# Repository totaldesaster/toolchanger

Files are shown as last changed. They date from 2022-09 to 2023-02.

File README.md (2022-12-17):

# Low-Cost Open Source Toolchanging mechanism for 3D printers

Magnetic tool changer project, inspired by E3D and Jubilee tool changing printers and designed for low cost and wide compatibility. My goal is to make toolchanging accessible without owning four figure machines.

# How does it work?




Both the tools and the toolhead have a circle of neodymium magnets with alternating north/south up polarities. Since opposing poles attract and same poles repel, the machine can switch between pulling and pushing on the tool by aligning the opposing or same poles of the magnets. This is done by a geared stepper motor on the toolhead which rotates the magnet circle (lockplate) - marked red and blue for north and south up in the first picture. Steel balls on the head and L profiles on the tool form a Maxwell coupling which ensures repeatable connections by having the tool contact the head in exactly 6 points - eliminating all 6 degrees of freedom, but not overconstraining the assembly, so there is theoretically exactly one position the tool can be in. The Klipper firmware is capable of controlling such a setup using the manual stepper feature and custom gcode macros. Similar features might exist in other firmwares as well.

# How do I use it?

Klipper code, CAD files and assembly drawings are documented on here. You'll need to design a carriage and dock base for your printer (please share with the community if you do!) and attach the components to it. Be aware that all of this is very experimental - you're welcome to test it and make any changes you want, but please note that this is not a finished product. I'm not responsible for any failures that may occur.

The 28BYJ-48 stepper motor can be driven with a normal stepstick with some minor modifications, you only need some basic tools. Follow the guide at https://www.youtube.com/watch?v=kq04-ReW1xY and wire it to a free stepper driver. This gives the motor more torque, which it needs to overcome the magnetic forces. Tools and extruders are wired the same way as in a standard multi extruder setup. Insert the magnets into the tools and lockplate, making sure to align the north/south poles so that the tool is pulled towards the lockplate when its "nose" is pointing straight up. Attach the tool head to the extruder carriage.

Attach a tool dock to the frame of your printer and make sure it is at the same height as the tools on the head. The holes at the bottom of the tool are supposed to slide over the pins of the dock when parking.



Modify your firmware with the toolchange code from this repository (currently only available for Klipper). Make sure you adjust the positions to suit your setup! Positions are best adjusted by moving the printer using G1 commands (G1 X10 Y50, for example) or whatever manual move command your printer may have. Make sure the head can clear any parked tools when moving to the next tool.

Slicer settings are the same as for normal multi extrusion printers, Klipper intercepts the T0/T1/... commands and adapts them to what the toolchanger needs.

# Versions

Currently, there are files for two versions on this repository. The prototype used pogo pins to electrically connect the tool, instead of wiring each tool individually. This has been more problematic than expected, so I discarded this for the "offical" V1 release. Mechanically, they are the same. More information is available in the prototype's readme.

# FAQs

Can I use this on my printer? What kind of tools can I use?

If your printer has a motion system that moves the head in both X and Y axes - such as a CoreXY - you only need a free stepper driver. Code is only available for Klipper right now, but it could probably be implemented in other firmwares too.
I recommend using only lightweight tools like Bowden hotends. The magnets aren't strong enough to reliably hold heavier tools. Tools like lasers or pen plotters are also possible, whatever you can design light enough can go on!

Why not use x instead?

A servo: For improved compatibility. Servos require a high current 5V power supply that's not available on all printers. Controlling it this way only needs a free motor driver.

Electromagnets: while they would work, they need to be constantly powered to keep holding the tool. That means the tool would fall off in the event of a power loss.

Permanent electromagnets: they're much heavier for the same force.

A physical lock: This would require precise parts that can't be produced on home 3D printers.

What happens if the nozzle hits a curled up edge?

From my testing so far, if it hits hard enough to overpower the magnets, it just flops up a little and then goes back on just fine. This actually makes it more resistant to print failures from what I've seen! If the tool falls off, there's a microswitch on the head that allows the controller to detect it (not yet implemented in software!).

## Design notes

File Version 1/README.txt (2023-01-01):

Below are the parts I used. See the assembly drawings for details. The included Klipper config is meant to serve as an example how to configure your machine and is not complete!

Toolhead:
Coupler Ball		https://de.aliexpress.com/item/32646556334.html?spm=a2g0o.order_list.0.0.21ef5c5fhdG5Fl&gatewayAdapt=glo2deu
KW11-3Z	Microswitch	https://de.aliexpress.com/item/1635599799.html?spm=a2g0o.order_list.0.0.21ef5c5fhdG5Fl&gatewayAdapt=glo2deu
28BYJ-48 Stepper	https://de.aliexpress.com/item/33061950792.html
Magnets			https://www.supermagnete.de/eng/disc-magnets-neodymium/disc-magnet-10mm-1.5mm_S-10-1.5-N52N

Tool:
Trianglelab Arethusa	https://de.aliexpress.com/item/32868524586.html?gatewayAdapt=glo2deu
Magnets			https://www.supermagnete.de/eng/disc-magnets-neodymium/disc-magnet-10mm-1.5mm_S-10-1.5-N52N
L profile		Doesn't matter too much - random bits I had laying around...

Printed parts:
I'd recommend printing all mechanical parts with at least 4 walls and 25% Infill. I used Extrudr PLA NX2 for mine, any decent quality filament should work.

You can use the Tool_Template files under Inventor Files / STEP Files to base your own tools on. If you designed heads or dock bases for your printer, please, feel free to share them!

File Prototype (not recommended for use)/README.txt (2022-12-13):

This version uses pogo pins on the toolhead to electrically connect the tool. These have proven to be more trouble than they’re worth. Do not use this version unless you intend to develop the idea further.

I had to disable thermistor protection features (disabled VERIFY_HEATER in Klipper and set MAXTEMP ridiculously high) to fool the firmware into accepting the tool change. I accomplished this by the microswitch connecting a resistor in parallel to the thermistor when the tool is disconnected. This version also limits you to using the same thermistor type on all tools (or you need to accept that tools report incorrect temperatures). This could be improved if you are more versed in firmware development than I am.

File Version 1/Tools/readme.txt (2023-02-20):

Note: some of the tools here are designed for an upside down toolhead (were originally designed for a printer with upside down head)

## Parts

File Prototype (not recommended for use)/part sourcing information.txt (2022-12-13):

Toolhead:
Coupler Ball		https://de.aliexpress.com/item/32646556334.html?spm=a2g0o.order_list.0.0.21ef5c5fhdG5Fl&gatewayAdapt=glo2deu
KW11-3Z			https://de.aliexpress.com/item/1635599799.html?spm=a2g0o.order_list.0.0.21ef5c5fhdG5Fl&gatewayAdapt=glo2deu
28BYJ-48		https://de.aliexpress.com/item/33061950792.html
S-10-1.5-N52N		https://www.supermagnete.de/eng/disc-magnets-neodymium/disc-magnet-10mm-1.5mm_S-10-1.5-N52N
419-10-206-00-006000	https://www.mouser.com/ProductDetail/Mill-Max/419-10-206-00-006000?qs=493kPxzlxfJDf1Hr1AIoOA%3D%3D
Bolts			Your local hardware store

Tool:
Trianglelab Arethusa	https://de.aliexpress.com/item/32868524586.html?gatewayAdapt=glo2deu
827-22-006-10-001101	https://www.mouser.com/ProductDetail/Mill-Max/827-22-006-10-001101?qs=aEjzgrpC3nabZ8NuQ8Fa5g%3D%3D
S-10-1.5-N52N		https://www.supermagnete.de/eng/disc-magnets-neodymium/disc-magnet-10mm-1.5mm_S-10-1.5-N52N
5mm magnet & L profile	Doesn't matter too much - random bits I had laying around...
Bolts			Your local hardware store
antclabs BLTouch	Your local 3D printer shop

Dock:
419-10-206-00-006000	https://www.mouser.com/ProductDetail/Mill-Max/419-10-206-00-006000?qs=493kPxzlxfJDf1Hr1AIoOA%3D%3D
Bolts & Dowel pins	Your local hardware store
5mm magnet		Doesn't matter too much - random bits I had laying around...

Printed parts:
I'd recommend printing all parts with at least 4 walls and 25% Infill. I used Extrudr PLA NX2 for mine, any decent quality filament should work.

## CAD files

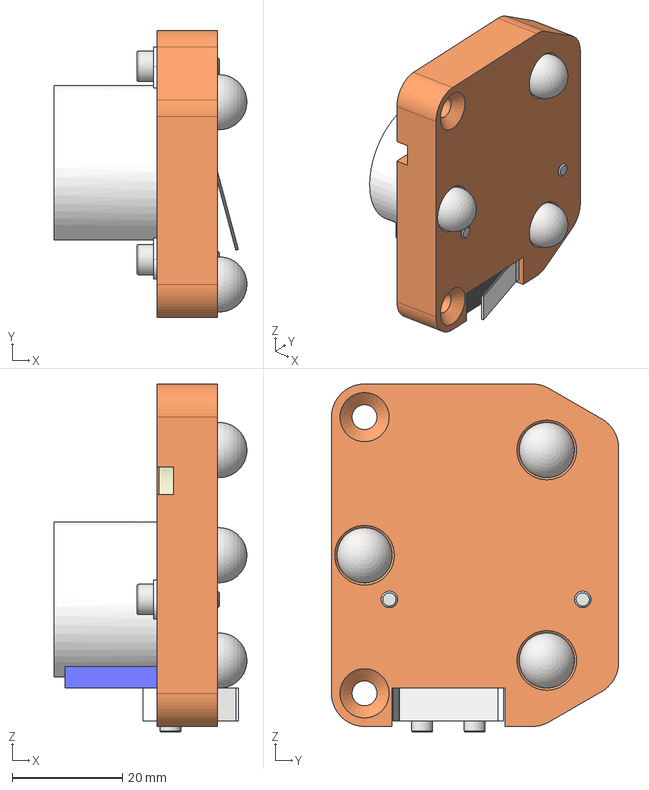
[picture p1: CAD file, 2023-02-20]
Version 1/STEP Files/Toolhead Assembly.stp
34.9 x 52.0 x 63.0 mm
MagToolChanger_Lockplate
MagToolChanger_HeadBase
28BYJ-48
RefSwitch_Basic
Magnet_10mm x 6
CouplerBall x 3
AS 1420 - 1973 - M3 x 12 x 2
ANSI B18.3.1M - M2x0.4 x 10, FSHCSM x 2
AS 1420 - 1973 - M4 x 8 x 2
ANSI B18.3.4M - M4 x 0.7 x 8, BHSBHCSM

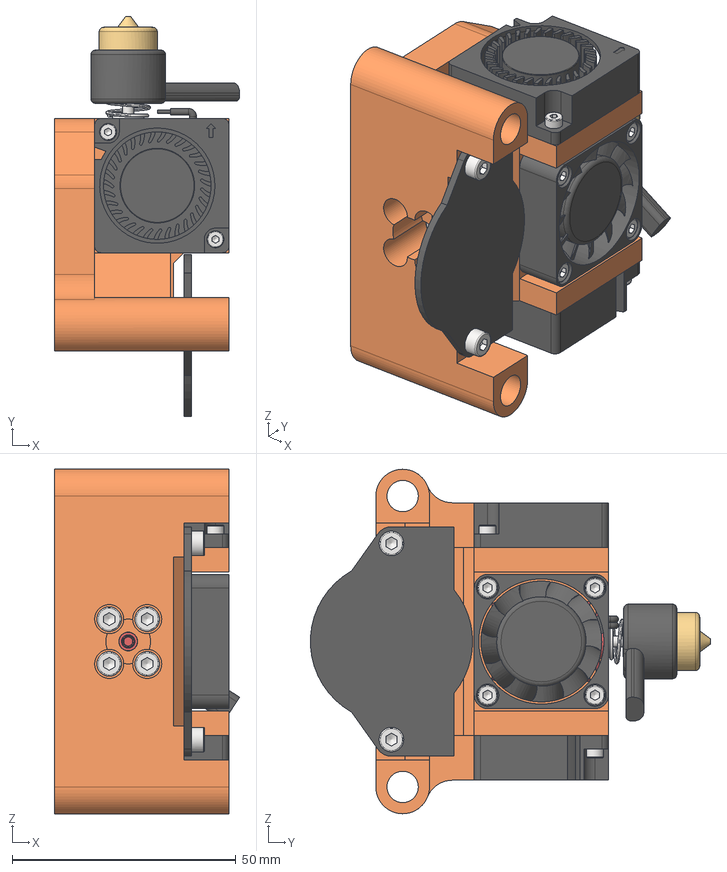
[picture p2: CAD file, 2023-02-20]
Version 1/Tools/Tool Assembly - E3D Revo CAN Bus.stp
41.4 x 89.4 x 77.0 mm
Tool_Revo_1
CouplerL x 3
Magnet_10mm x 6
Mellow Fly SHT36
30mm Fan Mockup 3010 x 2
3010 Вентилятор
Revo Voron Reference CAD
BS EN ISO 4762 - M2.5 x 12 x 4
BS EN ISO 4762 - M3 x 8 x 2
BS EN ISO 4762 - M3 x 12 x 4
BS EN ISO 4762 - M2 x 8 x 4

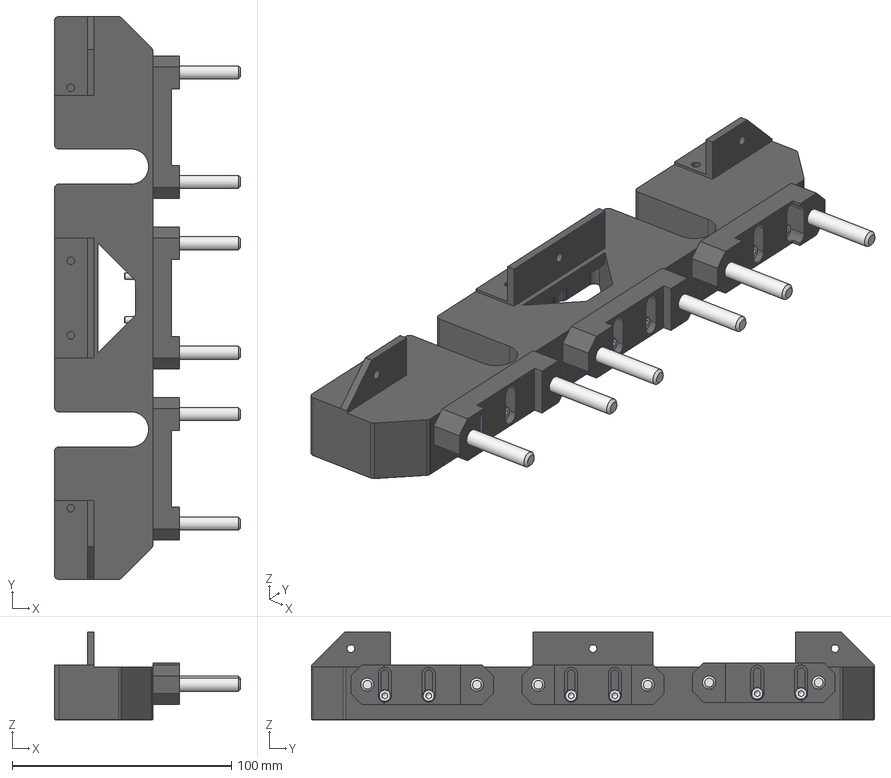
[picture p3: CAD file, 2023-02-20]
Version 1/STEP Files/Tool Dock Assembly.stp
85.0 x 257.0 x 40.0 mm
ToolDock_Base
ToolDock_Center
ToolDock_Left
ToolDock_R
AS 1420 - 1973 - M3 x 16 x 6
ToolDock_Bolt x 6

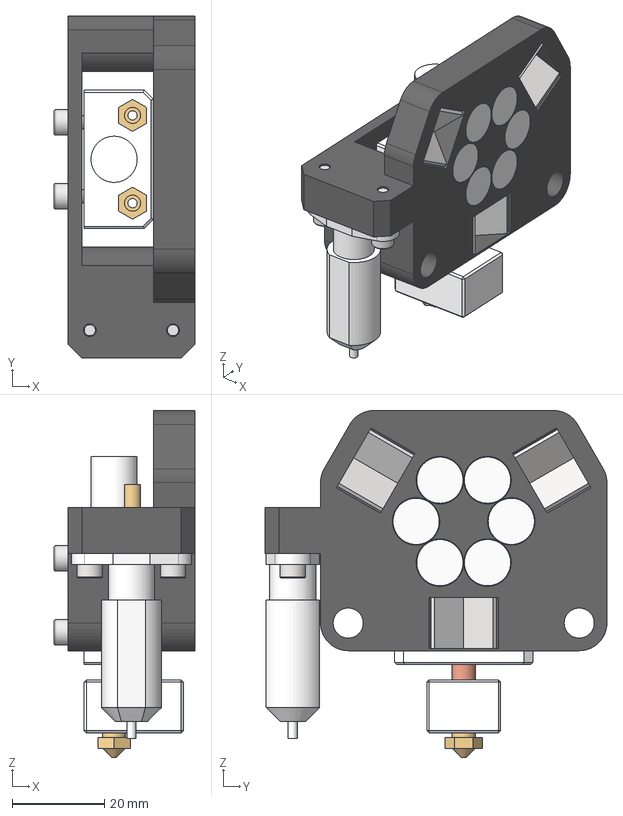
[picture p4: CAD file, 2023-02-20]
Version 1/Tools/Tool Assembly - Trianglelab Arethusa w BLTouch.stp
30.5 x 74.0 x 75.1 mm
MagToolChanger_Tool_1
CouplerL x 3
Magnet_10mm x 6
Arethusa
AS 1420 - 1973 - M3 x 8 x 4
BLTouch
AS 1420 - 1973 - M3 x 12 x 2

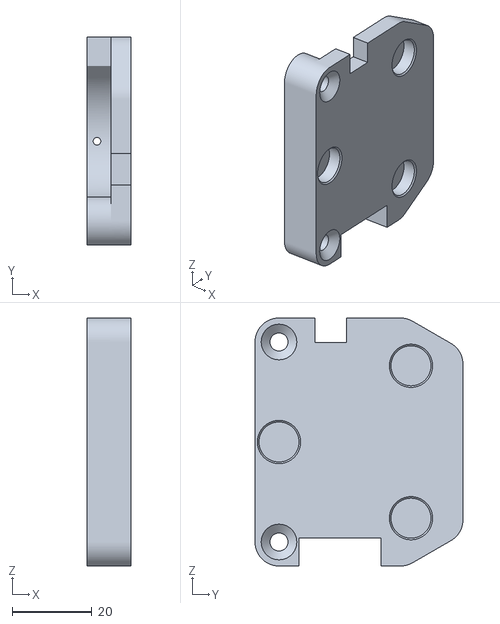
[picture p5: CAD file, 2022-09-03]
Prototype (not recommended for use)/STLs/TC_Head.stl
11.0 x 52.0 x 62.0

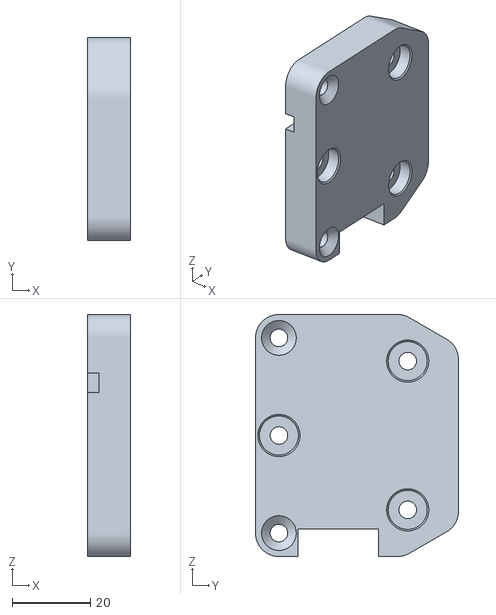
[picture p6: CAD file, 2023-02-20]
Version 1/STL Files/Head_Base.stl
11.0 x 52.0 x 62.0

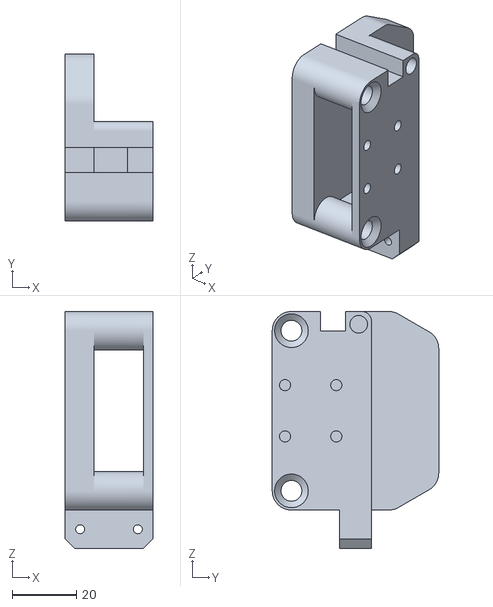
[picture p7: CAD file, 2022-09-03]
Prototype (not recommended for use)/STLs/TC_Tool_ArethusaBLT.stl
27.5 x 52.0 x 74.0

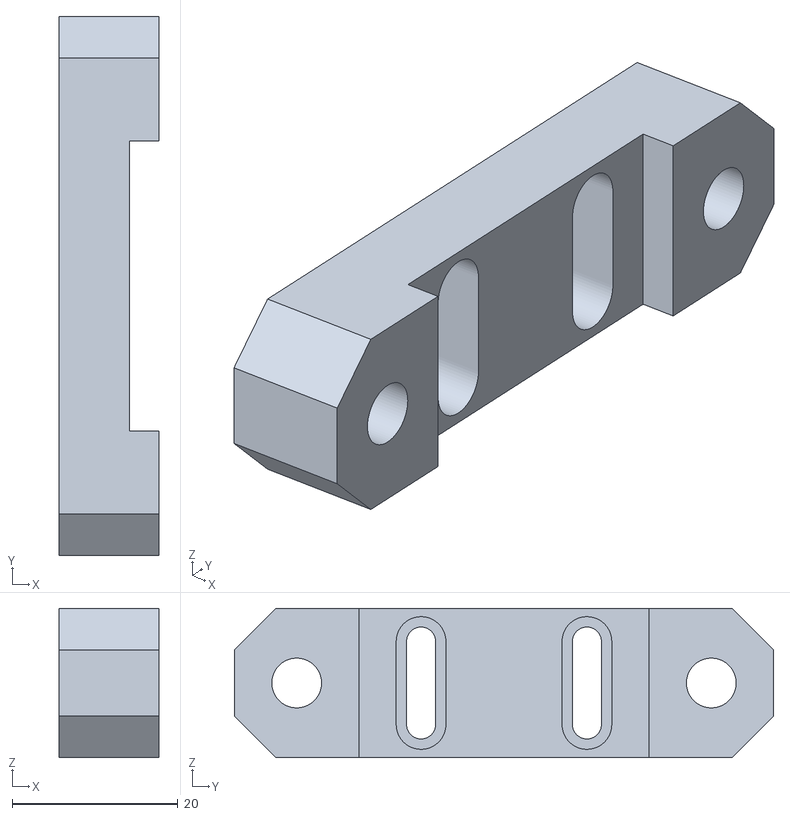
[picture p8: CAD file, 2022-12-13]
Version 1/STL Files/Dock_Center.stl
12.0 x 65.0 x 18.0

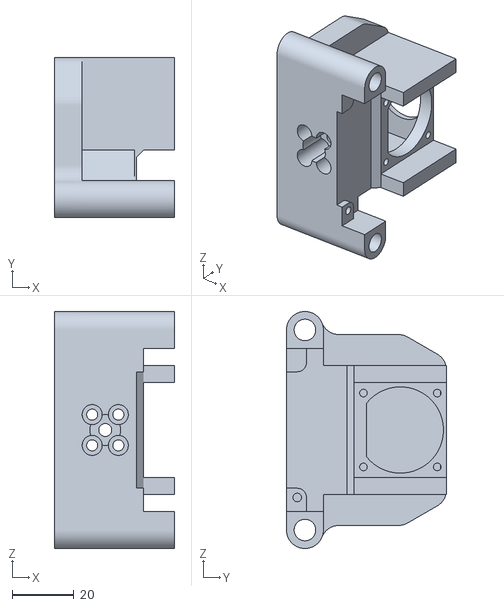
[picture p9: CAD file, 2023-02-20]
Version 1/Tools/Tool Base - E3D Revo CAN Bus.stl
39.0 x 52.0 x 77.0

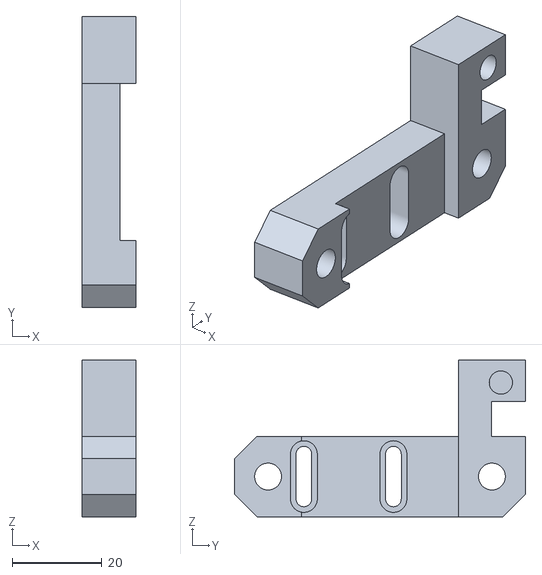
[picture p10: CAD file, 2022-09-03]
Prototype (not recommended for use)/STLs/TC_Dock_Left.stl
12.0 x 65.0 x 35.0

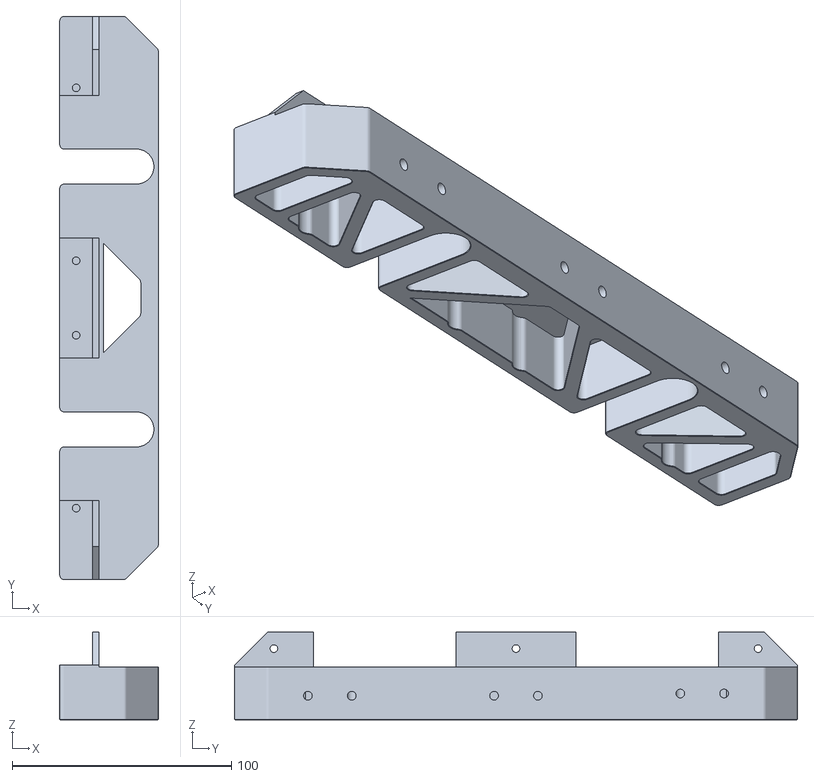
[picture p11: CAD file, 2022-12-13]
Version 1/STL Files/Dock_Base.stl
45.0 x 257.0 x 40.0

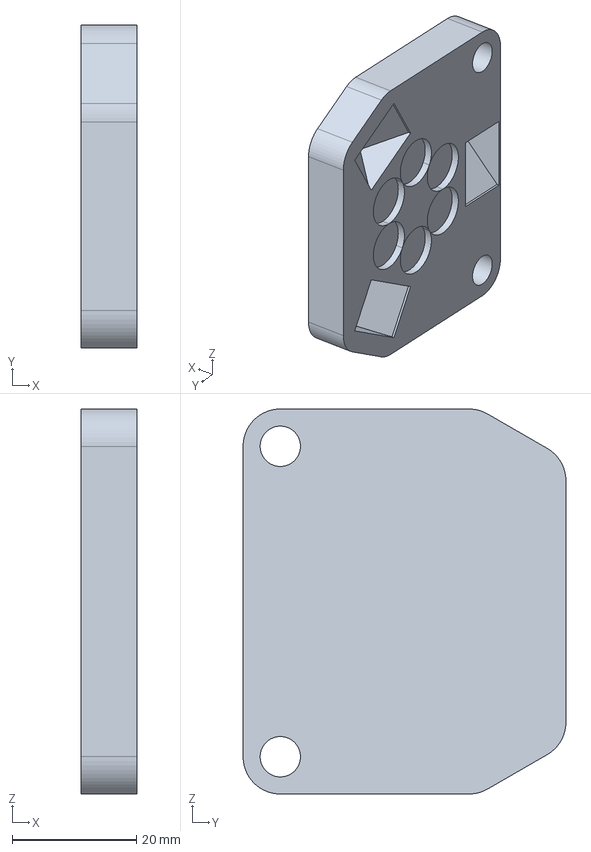
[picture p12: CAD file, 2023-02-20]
Version 1/Tools/Tool Template.stp
9.00 x 52.0 x 62.0 mm

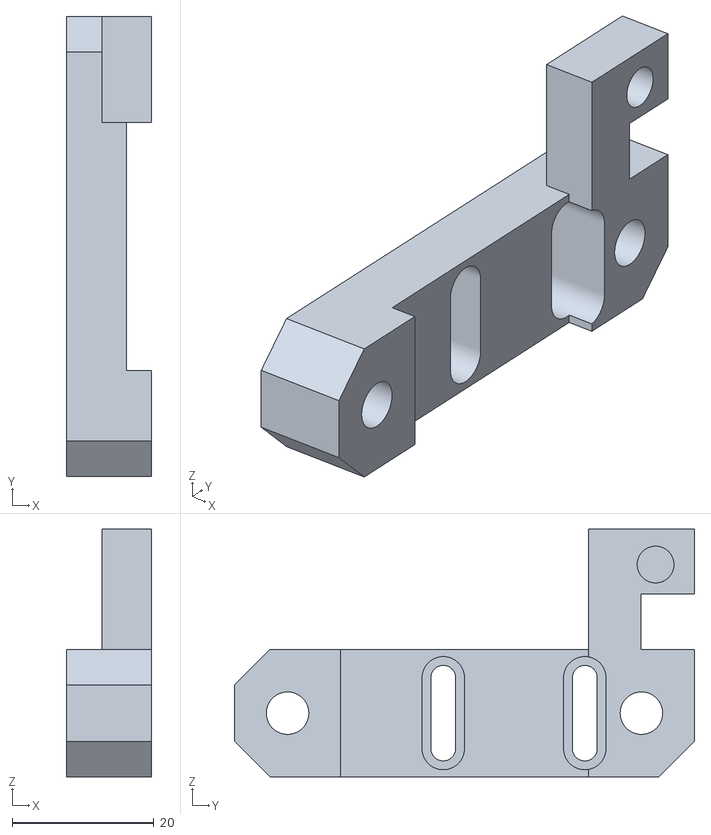
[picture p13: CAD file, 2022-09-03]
Prototype (not recommended for use)/STLs/TC_Dock_Right.stl
12.0 x 65.0 x 35.0

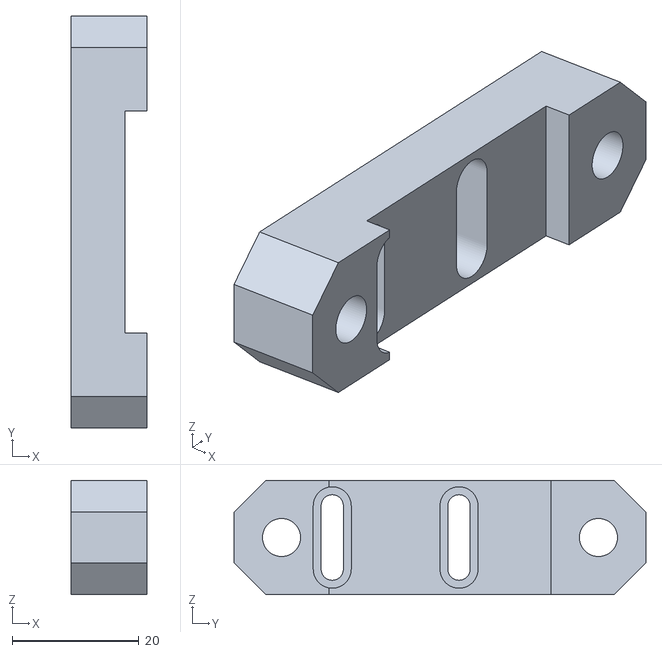
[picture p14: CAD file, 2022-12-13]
Version 1/STL Files/Dock_Left.stl
12.0 x 65.0 x 18.0

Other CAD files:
Prototype (not recommended for use)/STLs/TC_Lockplate.stl
Version 1/STL Files/Dock_Right.stl
Version 1/Tools/Tool Base - Trianglelab Arethusa w BLTouch.stl
Prototype (not recommended for use)/STLs/TC_Tool_Arethusa.stl
Prototype (not recommended for use)/STLs/TC_Dock_Base1515.stl
Prototype (not recommended for use)/STLs/TC_Dock_Center.stl
Version 1/Inventor Files/Dock/AS 1420 - 1973 - M3 x 16.ipt
Version 1/Inventor Files/Dock/ToolDock.iam
Version 1/Inventor Files/Dock/ToolDock_Base.ipt
Version 1/Inventor Files/Dock/ToolDock_Bolt.ipt
Version 1/Inventor Files/Dock/ToolDock_Center.ipt
Version 1/Inventor Files/Dock/ToolDock_Left.ipt
Version 1/Inventor Files/Dock/ToolDock_R.ipt
Version 1/Inventor Files/Head/ANSI B18.3.1M - M2x0.4 x 10(1).ipt
Version 1/Inventor Files/Head/ANSI B18.3.4M - M4 x 0.7 x 8(2).ipt
Version 1/Inventor Files/Head/AS 1420 - 1973 - M3 x 12.ipt
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

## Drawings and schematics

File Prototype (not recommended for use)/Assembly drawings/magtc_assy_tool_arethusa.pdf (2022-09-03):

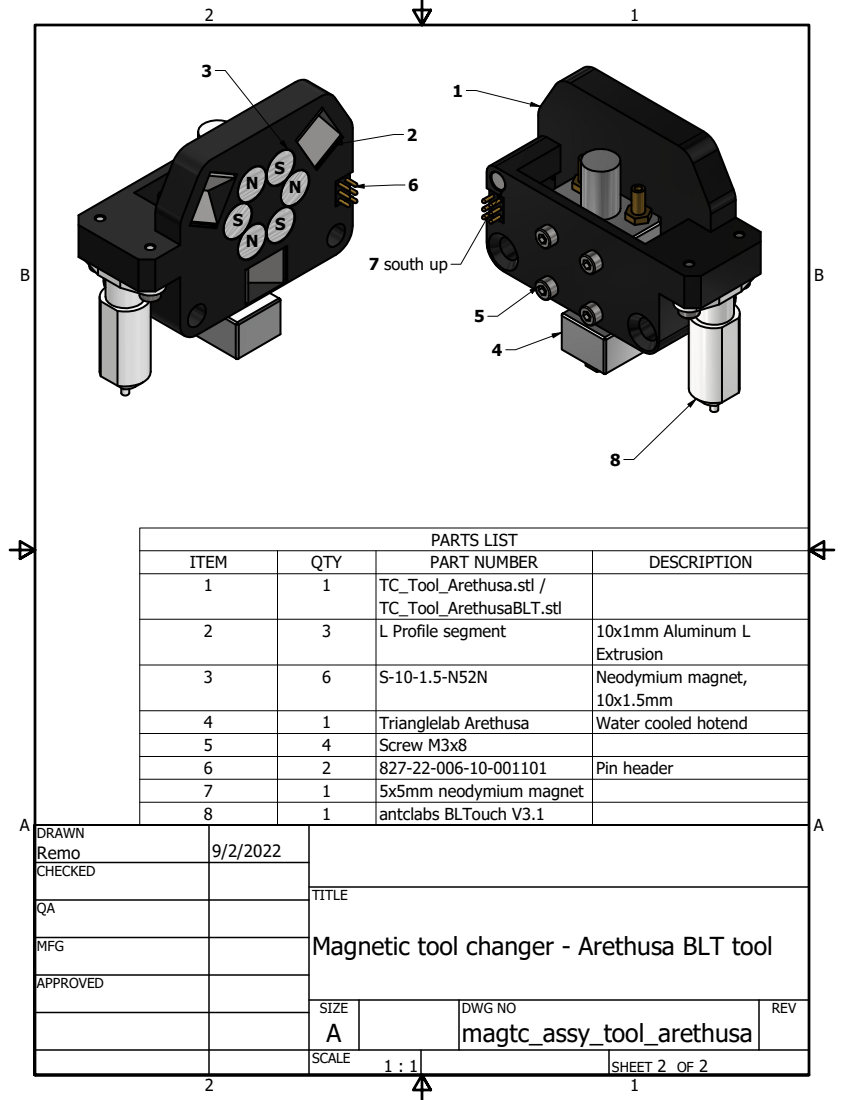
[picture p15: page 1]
PARTS LIST; 7 south up

ITEM | QTY | PART NUMBER | DESCRIPTION
1 | 1 | TC_Tool_Arethusa.stl / TC_Tool_ArethusaBLT.stl

2 | 3 | L Profile segment | 10x1mm Aluminum L Extrusion

3 | 6 | S-10-1.5-N52N | Neodymium magnet, 10x1.5mm

4 | 1 | Trianglelab Arethusa | Water cooled hotend
5 | 4 | Screw M3x8
6 | 2 | 827-22-006-10-001101 | Pin header
7 | 1 | 5x5mm neodymium magnet
8 | 1 | antclabs BLTouch V3.1

DRAWN Remo | 9/2/2022

CHECKED

TITLE
Magnetic tool changer - Arethusa BLT tool

MFG

APPROVED

SIZE A | DWG NO magtc_assy_tool_arethusa | REV

SCALE 1 : 1 | | SHEET 2 OF 2

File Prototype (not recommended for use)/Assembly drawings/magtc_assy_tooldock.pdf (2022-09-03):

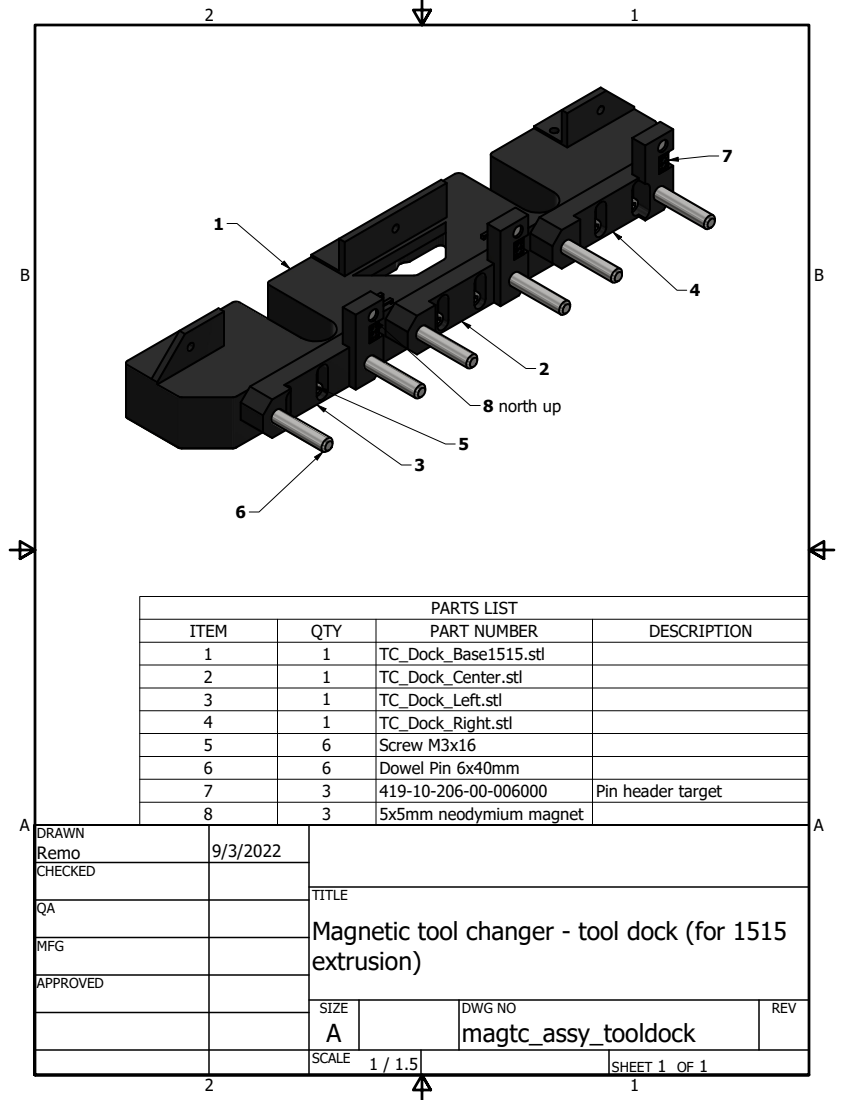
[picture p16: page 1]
PARTS LIST; 8 north up

ITEM | QTY | PART NUMBER | DESCRIPTION
1 | 1 | TC_Dock_Base1515.stl
2 | 1 | TC_Dock_Center.stl
3 | 1 | TC_Dock_Left.stl
4 | 1 | TC_Dock_Right.stl
5 | 6 | Screw M3x16
6 | 6 | Dowel Pin 6x40mm
7 | 3 | 419-10-206-00-006000 | Pin header target
8 | 3 | 5x5mm neodymium magnet

DRAWN Remo | 9/3/2022

CHECKED

TITLE
Magnetic tool changer - tool dock (for 1515
extrusion)

MFG

APPROVED

SIZE A | DWG NO magtc_assy_tooldock | REV

SCALE 1 / 1.5 | | SHEET 1 OF 1

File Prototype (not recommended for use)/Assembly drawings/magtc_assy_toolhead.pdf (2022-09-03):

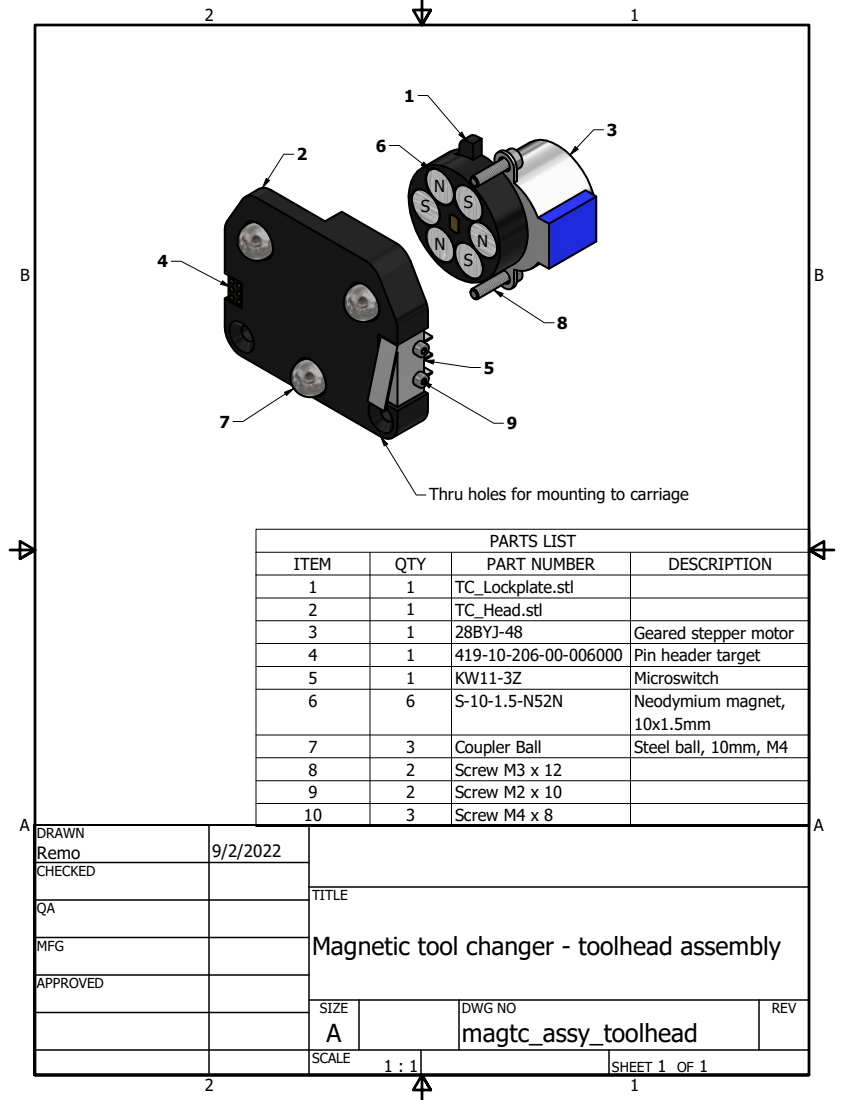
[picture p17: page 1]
PARTS LIST

Thru holes for mounting to carriage

ITEM | QTY | PART NUMBER | DESCRIPTION
1 | 1 | TC_Lockplate.stl
2 | 1 | TC_Head.stl
3 | 1 | 28BYJ-48 | Geared stepper motor
4 | 1 | 419-10-206-00-006000 | Pin header target
5 | 1 | KW11-3Z | Microswitch
6 | 6 | S-10-1.5-N52N | Neodymium magnet, 10x1.5mm

7 | 3 | Coupler Ball | Steel ball, 10mm, M4
8 | 2 | Screw M3 x 12
9 | 2 | Screw M2 x 10
10 | 3 | Screw M4 x 8

DRAWN Remo | 9/2/2022

CHECKED

TITLE
Magnetic tool changer - toolhead assembly

MFG

APPROVED

SIZE A | DWG NO magtc_assy_toolhead | REV

SCALE 1 : 1 | | SHEET 1 OF 1

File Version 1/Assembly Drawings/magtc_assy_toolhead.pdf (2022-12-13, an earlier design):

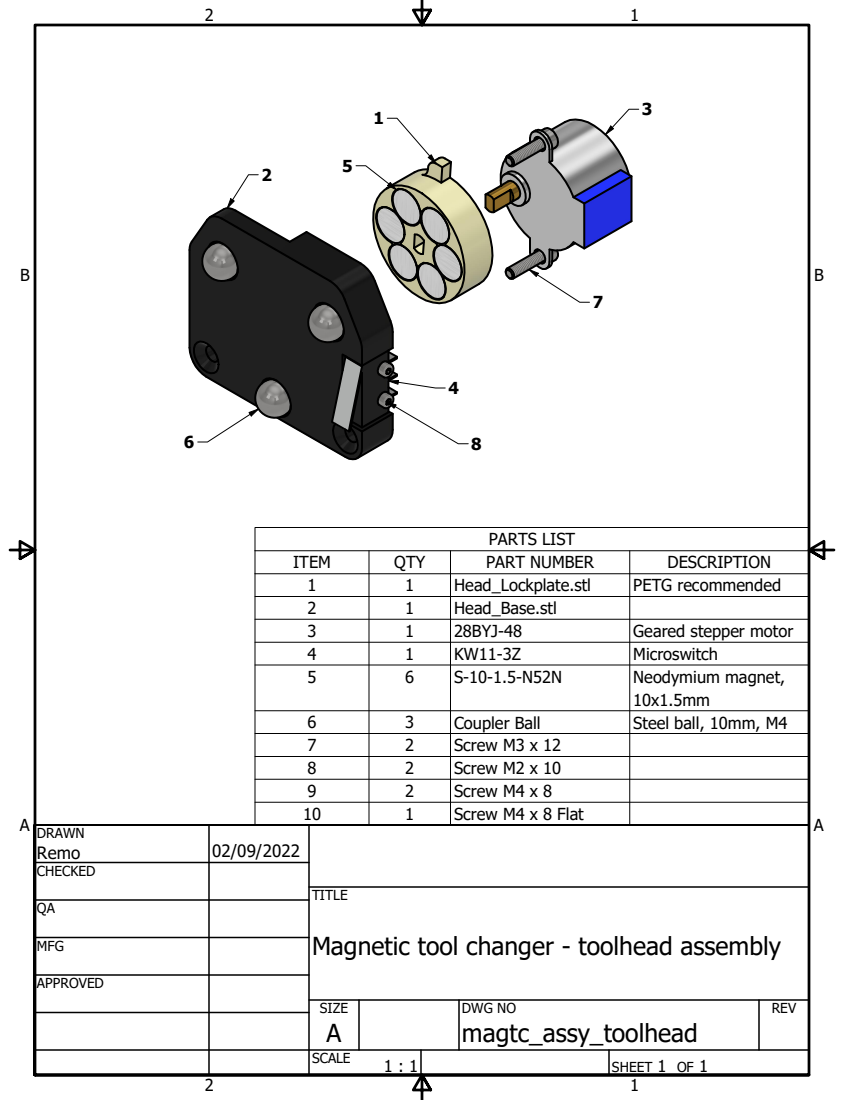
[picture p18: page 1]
PARTS LIST

ITEM | QTY | PART NUMBER | DESCRIPTION
1 | 1 | Head_Lockplate.stl | PETG recommended
2 | 1 | Head_Base.stl
3 | 1 | 28BYJ-48 | Geared stepper motor
4 | 1 | KW11-3Z | Microswitch
5 | 6 | S-10-1.5-N52N | Neodymium magnet, 10x1.5mm

6 | 3 | Coupler Ball | Steel ball, 10mm, M4
7 | 2 | Screw M3 x 12
8 | 2 | Screw M2 x 10
9 | 2 | Screw M4 x 8
10 | 1 | Screw M4 x 8 Flat

DRAWN Remo | 02/09/2022

CHECKED

TITLE
Magnetic tool changer - toolhead assembly

MFG

APPROVED

SIZE A | DWG NO magtc_assy_toolhead | REV

SCALE 1 : 1 | | SHEET 1 OF 1

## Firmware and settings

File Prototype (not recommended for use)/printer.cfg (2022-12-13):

# Insert these config file entries into your printer.cfg file. This is NOT a complete config file, only the entries required for the tool changer!



# Defines the toolhead stepper as a manual_stepper to allow direct control.
[manual_stepper toolhead]
step_pin: PE2
dir_pin: PE3
enable_pin: !PD4
microsteps: 16
rotation_distance: 5.625
full_steps_per_rotation: 200
velocity: 5
accel: 1000



# Example dual-extruder configuration for the "pogo pin head". Can be expanded by copying the config for the second extruder. If you're using tools connected normally by cables, define them normally as [extruder], [extruder1] etc instead.
[extruder]
# "Master" extruder. This is what the firmware uses to generate the move commands, includes the first feeder motor and heater.
step_pin: PF9
dir_pin: PF10
enable_pin: !PG2
sensor_pin: PF3
heater_pin: PA2
microsteps: 16
rotation_distance: 15.4
full_steps_per_rotation: 400
nozzle_diameter: 0.4
filament_diameter: 1.75
max_extrude_cross_section: 1
instantaneous_corner_velocity: 1.000
max_extrude_only_distance: 800
max_extrude_only_velocity: 100
max_extrude_only_accel: 1000
pressure_advance: 0.0
pressure_advance_smooth_time: 0.040
max_power: 1.0
sensor_type: PT1000
pullup_resistor: 4700
smooth_time: 1.0
control: pid
pid_Kp: 22
pid_Ki: 1
pid_Kd: 114
pwm_cycle_time: 0.100
min_extrude_temp: 170
min_temp: -100
max_temp: 400

[extruder_stepper extruder1]
# Second feeder motor. Does NOT generate motion commands, will be synchronized to the first extruder motion queue on demand.
extruder: extruder
step_pin: PC13
dir_pin: PF0
enable_pin: !PF1
microsteps: 16
rotation_distance: 15.4
full_steps_per_rotation: 400

[heater_generic extruder1]
# Stand-by dock heater. Takes any temperature commands that are not directed to T0.
gcode_id: T1
sensor_pin: PF4
heater_pin: PA3
sensor_type: PT1000
pullup_resistor: 4700
smooth_time: 1.0
max_power: 0.7
control: pid
pid_Kp: 22
pid_Ki: 1
pid_Kd: 114
pwm_cycle_time: 0.100
min_temp: -100
max_temp: 400

[tmc2209 manual_stepper toolhead]
# Motor driver for the toolhead motor. 300mA is running the motor hard, but since it only runs in short bursts it can take this temporary overload without overheating.
uart_pin: PE1
interpolate: True
run_current: 0.3
hold_current: 0.1
stealthchop_threshold: 0



# G-Code Macros used to control the tool change. Use these for Pogo Pin tools. Macros for directly wired tools are below. This example uses two extruders and an additional "dumb" tool (e.g. pen plotter)
[gcode_macro TOOLCHANGE]
description: evaluate and execute tool change
variable_current_tool: 0
variable_next_tool: 0
gcode:
    # Evaluate what tool is currently on the head
    {% set old_tool = printer["gcode_macro TOOLCHANGE"].current_tool|default(0)|int %}
    # Evaluate next tool to pick up, use the passed value if TOOL call was passed, otherwise use the stored next tool
    {% if 'TOOL' in params %}
        {% set new_tool = params.TOOL|default(0)|int %}
        SET_GCODE_VARIABLE MACRO=TOOLCHANGE VARIABLE=current_tool VALUE={params.TOOL}
    {% else %}
        {% set new_tool = printer["gcode_macro TOOLCHANGE"].next_tool|default(0)|int %}
        SET_GCODE_VARIABLE MACRO=TOOLCHANGE VARIABLE=current_tool VALUE={printer["gcode_macro TOOLCHANGE"].next_tool}
    {% endif %}
    # Check for needless tool change
    {% if old_tool == new_tool %}
        {action_respond_info("Requested tool is already mounted, not doing tool change!")}
    {% else %}
        # Move to the pre-park position depending on what tool is mounted, desynchronize parked extruder from motion queue
        {% if old_tool == 0 %}
            G1 Y190 X5 F10000
            SYNC_EXTRUDER_MOTION EXTRUDER=extruder MOTION_QUEUE=
        {% elif old_tool == 1 %}
            G1 Y97.7 X5 F10000
            SYNC_EXTRUDER_MOTION EXTRUDER=extruder1 MOTION_QUEUE=
        {% elif old_tool == 2 %}
            G1 Y20 X5 F10000
            # T2 is not an extruder, not synchronizing to queue
        {% endif %}
        # Park the tool
        G1 X-23 F1500
        MANUAL_STEPPER STEPPER=toolhead ENABLE=1
        MANUAL_STEPPER STEPPER=toolhead MOVE=10 SPEED=15
        MANUAL_STEPPER STEPPER=toolhead ENABLE=0
        G1 X5 F5000
        # Move to the pre-pick position depending on what tool is requested, synchronize new extruder to motion queue 
        {% if new_tool == 0 %}
            G1 Y190
            SYNC_EXTRUDER_MOTION EXTRUDER=extruder MOTION_QUEUE=extruder
            SET_GCODE_OFFSET Z=0
            SET_GCODE_OFFSET Y=0
            SET_GCODE_OFFSET X=0
        {% elif new_tool == 1 %}
            G1 Y97.7
            SYNC_EXTRUDER_MOTION EXTRUDER=extruder1 MOTION_QUEUE=extruder
            SET_GCODE_OFFSET Z=0
            SET_GCODE_OFFSET Y=0
            SET_GCODE_OFFSET X=0
        {% elif new_tool == 2 %}
            G1 Y20
            # T2 is not an extruder, not synchronizing to queue
            SET_GCODE_OFFSET Z=0
            SET_GCODE_OFFSET Y=0
            SET_GCODE_OFFSET X=0
        {% endif %}
        # Pick the tool
        G1 X-23 F1500
        G1 X-25 F500
        MANUAL_STEPPER STEPPER=toolhead ENABLE=1
        MANUAL_STEPPER STEPPER=toolhead MOVE=0 SPEED=15
        MANUAL_STEPPER STEPPER=toolhead ENABLE=0
        G1 X5 F5000
    {% endif %}

[gcode_macro ACTIVATE_EXTRUDER]
description: Klipper-Style Alias for TOOLCHANGE macro
rename_existing: ACTIVATE_EXTRUDER_BASE
gcode:
    {% set ext = params.EXTRUDER|default(EXTRUDER) %}
    {% if ext == "extruder" %}
        TOOLCHANGE TOOL=0
    {% elif ext == "extruder1" %}
        TOOLCHANGE TOOL=1
    {% else %}
        TOOLCHANGE TOOL=2
    {% endif %}
    
[gcode_macro T0]
description: CNC-Style Alias for TOOLCHANGE macro
gcode:
    TOOLCHANGE TOOL=0

[gcode_macro T1]
description: CNC-Style Alias for TOOLCHANGE macro
gcode:
    TOOLCHANGE TOOL=1

[gcode_macro T2]
description: CNC-Style Alias for TOOLCHANGE macro
gcode:
    TOOLCHANGE TOOL=2
    
[gcode_macro M104]
description: Change "T" Calls in M104 commands to Head/Standby instead of T0/T1
rename_existing: M104.1
gcode:
    {% set s = params.S|default(0)|float %}
    {% set t = params.T|default(0)|int %}
    {% set current_tool = printer["gcode_macro TOOLCHANGE"].current_tool|default(0)|int %}
    {%  if 'T' in params %}
        {%  if t == current_tool %}
            # use the temperature for the head
            M104.1 S{s}
        {% else %}
            # use the temperature for the standby heater
            SET_HEATER_TEMPERATURE HEATER=extruder1 TARGET={s}
	    # add any additional standby heaters here!
        {% endif %}
    {% else %}
            # assume Head if no tool is given
            M104.1 S{s}
    {% endif %}
    
[gcode_macro M109]
description: Change "T" Calls in M109 commands to Head/Standby instead of T0/T1
rename_existing: M109.1
gcode:
    {% set s = params.S|default(0)|float %}
    {% set t = params.T|default(0)|int %}
    {% set current_tool = printer["gcode_macro TOOLCHANGE"].current_tool|default(0)|int %}
    {%  if 'T' in params %}
        {%  if t == current_tool %}
            # use the temperature for the head
            M109.1 S{s}
        {% else %}
            # use the temperature for the standby heater
            SET_HEATER_TEMPERATURE HEATER=extruder1 TARGET={s}
	    # add any additional standby heaters here!
        {% endif %}
    {% else %}
        # assume Head if no tool is given
        M109.1 S{s}
    {% endif %}
    
[delayed_gcode activate_default_extruder]
# activate the default extruder at startup, assume tool 0 is mounted
initial_duration: 1
gcode:
    SYNC_EXTRUDER_MOTION EXTRUDER=extruder MOTION_QUEUE=extruder
    SYNC_EXTRUDER_MOTION EXTRUDER=extruder1 MOTION_QUEUE=
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

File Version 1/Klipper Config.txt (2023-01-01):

# Example configuration entries for tool changer



[extruder]
# Configure like a normal multi-extruder Klipper setup

[extruder1]
# Configure like a normal multi-extruder Klipper setup

# Don't add any entries for "non extruder" tools like a pen
# Haven't figured out how to add things like lasers yet...



# example manual stepper for the toolhead
[manual_stepper toolhead]
step_pin: PE2
dir_pin: PE3
enable_pin: !PD4
microsteps: 16
rotation_distance: 5.625
full_steps_per_rotation: 200
velocity: 5
accel: 1000

# example manual stepper TMC driver (name must be the same as the stepper it's assigned to)
[tmc2209 manual_stepper toolhead]
uart_pin: PE1
interpolate: True
run_current: 0.2
hold_current: 0.2
stealthchop_threshold: 0



[gcode_macro TOOLCHANGE]
description: execute the tool change, positions have to be adjusted for your machine!
variable_current_tool: 0
variable_next_tool: 0
gcode:
	# Reset all the offsets for parking
    SET_GCODE_OFFSET Z=0
    SET_GCODE_OFFSET Y=0
    SET_GCODE_OFFSET X=0
	
    # Evaluate what tool is currently on the head
    {% set old_tool = printer["gcode_macro TOOLCHANGE"].current_tool|default(0)|int %}
	
    # Evaluate next tool to pick up
    {% if 'TOOL' in params %}
        {% set new_tool = params.TOOL|default(0)|int %}
        SET_GCODE_VARIABLE MACRO=TOOLCHANGE VARIABLE=current_tool VALUE={params.TOOL}
    {% endif %}
	
    # Check for needless tool change (new tool = old tool)
    {% if old_tool == new_tool %}
        {action_respond_info("Requested tool is already mounted, not doing tool change!")}
    {% else %}
	
        # Move to the pre-park position depending on what tool is mounted
		# ADJUST THE POSITIONS HERE, straight ahead of the parking position, with clearance to pass other tools when moving sideways
        {% if old_tool == 0 %}
            G1 Y189 X5 F10000
        {% elif old_tool == 1 %}
            G1 Y97.2 X5 F10000
        {% elif old_tool == 2 %}
            G1 Y20 X5 F10000
        {% endif %}
		
        # Park the tool
		# ADJUST THE POSITIONS HERE, a few mm ahead of hitting the wall of the dock
        G1 X-21 F1500
        MANUAL_STEPPER STEPPER=toolhead ENABLE=1
        MANUAL_STEPPER STEPPER=toolhead MOVE=8 SPEED=15
		# ADJUST THE POSITIONS HERE, same as the X position in the pre-park position above
        G1 X5 F5000
        MANUAL_STEPPER STEPPER=toolhead ENABLE=0
		
        # Move to the pre-pick position depending on what tool is requested, synchronize new extruder to motion queue 
		# ADJUST THE POSITIONS HERE, straight ahead of the parking position
        {% if new_tool == 0 %}
            G1 Y189
            ACTIVATE_EXTRUDER EXTRUDER=extruder
        {% elif new_tool == 1 %}
            G1 Y97.7
            ACTIVATE_EXTRUDER EXTRUDER=extruder1
        {% elif new_tool == 2 %}
            G1 Y20
            # Example non-extruder tool - add any servos etc here as necessary
        {% endif %}
		
        # Pick the tool
        MANUAL_STEPPER STEPPER=toolhead ENABLE=1
		# ADJUST THE POSITIONS HERE, just before hitting the tool dock wall
        G1 X-23 F1500
        G1 X-24 F500
        MANUAL_STEPPER STEPPER=toolhead MOVE=0 SPEED=15
        MANUAL_STEPPER STEPPER=toolhead ENABLE=0
        G1 X10 F5000
    {% endif %}
	
    # Apply offsets
	# ADJUST THE POSITIONS HERE, offsets to make sure the nozzles are aligned to each other
    {% if new_tool == 0 %}
        SET_GCODE_OFFSET Z=1.1
        SET_GCODE_OFFSET Y=0
        SET_GCODE_OFFSET X=15
    {% elif new_tool == 1 %}
        SET_GCODE_OFFSET Z=0.75
        SET_GCODE_OFFSET Y=0.3
        SET_GCODE_OFFSET X=14.8
    {% elif new_tool == 2 %}
        SET_GCODE_OFFSET Z=0
        SET_GCODE_OFFSET Y=0
        SET_GCODE_OFFSET X=0
    {% endif %}
    
	
	
[gcode_macro T0]
description: CNC-Style Alias for TOOLCHANGE macro
gcode:
    TOOLCHANGE TOOL=0

[gcode_macro T1]
description: CNC-Style Alias for TOOLCHANGE macro
gcode:
    TOOLCHANGE TOOL=1

[gcode_macro T2]
description: CNC-Style Alias for TOOLCHANGE macro
gcode:
    TOOLCHANGE TOOL=2
    
    	
	
[delayed_gcode activate_default_extruder]
# activate the default extruder at startup, assume tool 0 is mounted
initial_duration: 1
gcode:
    T0

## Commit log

2022-09-03 Added mechanical documentation for v1 prototype
    [TC_Dock_Base1515.stl, TC_Dock_Center.stl, TC_Dock_Left.stl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]
2022-12-13 Version 1 release (mechanical)
    Added drawings and CAD files for version 1
    [ANSI (in).dwg, ANSI (in).idw, ANSI (mm).dwg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]
2022-12-13 Updated Prototype information
    [TC_Dock_Base1515.stl, TC_Dock_Center.stl, TC_Dock_Left.stl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]
2023-01-01 CAD File cleanup, added firmware code
    [ANSI (in).dwg, ANSI (in).idw, ANSI (mm).dwg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]
2023-02-20 Minor changes on head, file cleanup
    [Dock_Base.stp, Dock_Center.stp, Dock_Left.stp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]
2023-02-20 Added Revo tool
    [Tool Assembly - E3D Revo CAN Bus.stp, Tool Assembly - Trianglelab Arethusa w BLTouch.stp, Tool Base - E3D Revo CAN Bus.stl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]
